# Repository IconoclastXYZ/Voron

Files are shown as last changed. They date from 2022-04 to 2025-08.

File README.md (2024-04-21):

# Voron
Build details, tips, tricks and traps for the 2.4 r1 - r2

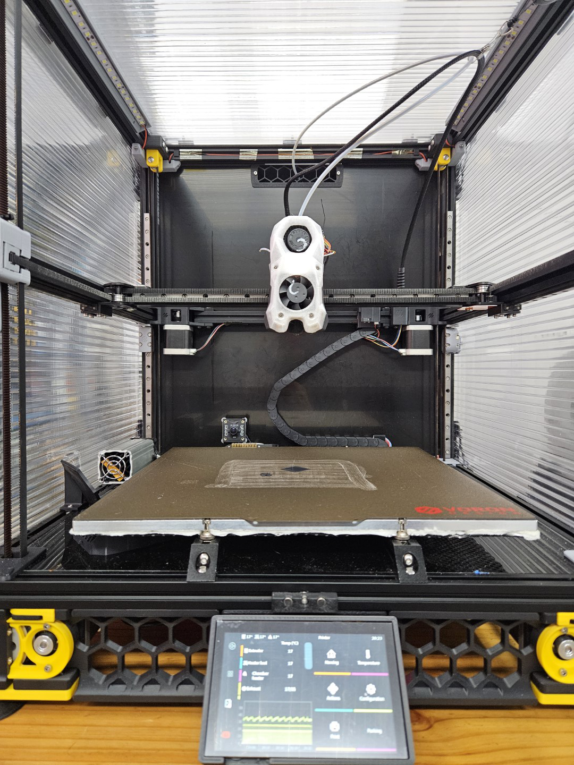
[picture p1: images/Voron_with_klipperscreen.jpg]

Closeup of the active heater with the angled air flow diverter
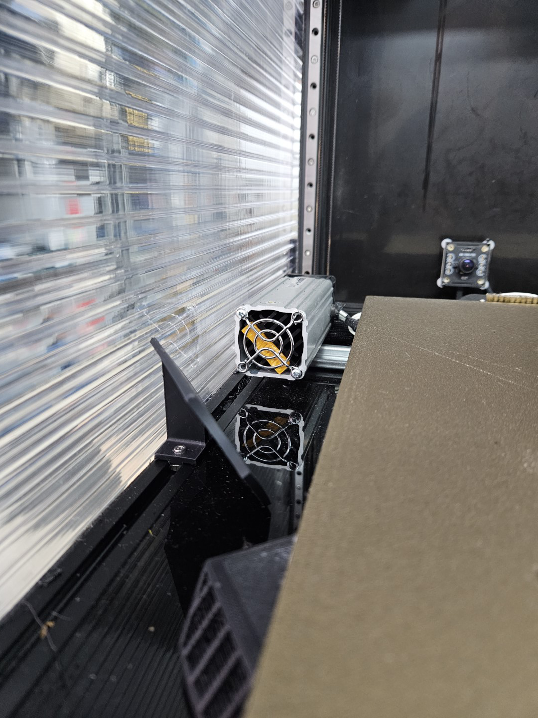
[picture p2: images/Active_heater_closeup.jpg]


With a hotmesh from the finished printer

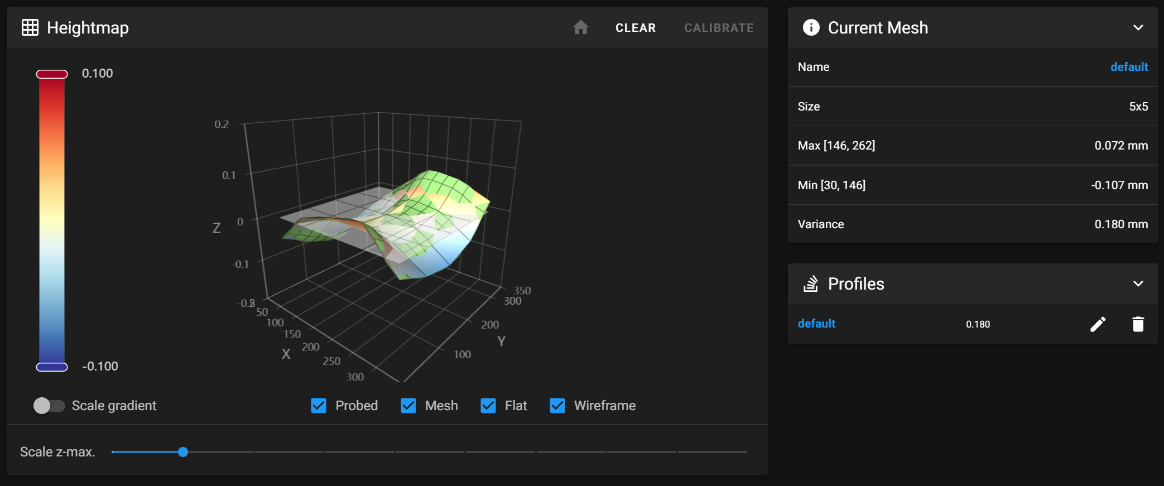
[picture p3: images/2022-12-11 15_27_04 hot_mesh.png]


## Base build from Formbot 3D kit - There were a few traps for young players in the Formbot 3D build, outlined [here](https://github.com/IconoclastXYZ/Voron/blob/main/articles/formbot_build.md)

## Things I wish I had known BEFORE starting to assemble the Voron
Lots of others build lists and hints exist, with my particular blind spots / learning points listed [here](https://github.com/IconoclastXYZ/Voron/blob/main/articles/build_lessons.md)
  
## [My current setup](https://github.com/IconoclastXYZ/Voron/blob/main/articles/my_setup.md)  

## Remember
- After each toolhead change (nozzle, fan replacement, heater change) run `PROBE_CALIBRATE` and remember to do it at a baked temp (nozzle 240, bed 95) and then do `TESTZ Z=-0.1` when happy with the paper test as Klipper assumes you do it [cold](https://docs.vorondesign.com/build/startup/#z-offset-adjustment)
  
## ToDo
- Fix the `controller_fan.py` script so that controller fans do not always come on with any stepper motor - to replace the kludge using a fake stepper motor
  
## Under consideration
- [Plug panel](https://github.com/tanaes/whopping_Voron_mods/blob/main/side_skirts/STLs/side_skirt-plug_panel-350.stl) for external connections to the Pi, but need to find out what the holes are sized for?
- [Full coverage heater pad](https://uniqueprints.shop/shop/buildplate/voron-keenovo-bed-heater-fermio/)
- [Custom heater plate with slot for top of plate temperature sensor](https://preciseprinterparts.com/voron-cast-aluminum-printer-bed-350mm-vor-ver-24-and-18.html)
- [Kinematic bed mount](https://github.com/tanaes/whopping_Voron_mods/tree/main/kinematic_bed)
- [FYSETC ultralight X rail](https://www.aliexpress.us/item/3256804719096286.html) with the appropriate mounting blocks from [here](https://github.com/GiulianoM/Fystec-Voron-X-Block), [here](https://www.thingiverse.com/thing:5671339) or [here](https://www.teamfdm.com/files/file/641-light-x-beam-mounting-block/), with the [M5 heat inserts](https://www.amazon.com/M5x5-8mm-OD7-1mm-Threaded-Plastic-Staking/dp/B08T9W17CR)
  
## Utility and Test prints
- Voron test cube
- [Andrew Ellis print tuning guide and parts](https://ellis3dp.com/Print-Tuning-Guide/)
- [Eric Zimmerman setup guides and Voron config](https://github.com/EricZimmerman/VoronTools)
- [X-rail belt clamps for installing the toolhead easily](https://www.printables.com/model/714602-voron24trident-ab-belt-clamps-reoriented-and-holes/files)
- [Filament swatches](https://www.printables.com/model/27814)
- [Bridging tests](https://www.thingiverse.com/thing:476845/files)
- [Temperature tower models](https://www.thingiverse.com/thing:2729076)
- [Hot end flow test generator](https://hotend-flow-tester.netlify.app/)
- [Pressure advance calibration pattern generator](https://realdeuce.github.io/Voron/PA/pressure_advance.html)
- [Variety of Wago mounts](https://github.com/VoronDesign/VoronUsers/tree/master/printer_mods/LoganFraser/WagoMounts)

## [Filament settings for the Voron](/filaments/Polymaker-filament-settings.md)
- Filament dryer (a must!) - [EIBOS 3D Filament Dryer CYCLOPES](https://www.eibos3d.com/cyclopes-detail) - there are quite a few alternatives, but none of them seem to work terribly well. This one regularly gets the filaments down to 20% RH
- Polymaker Polylite PA6-CF
- Polymaker Polylite ASA
- Polymaker Polylite PLA
- Polymaker Polylite PC

## Other resources
- [BTT Octopus pinout](https://github.com/VoronDesign/VoronUsers/tree/master/firmware_configurations/klipper/revnull/btt_octopus_pins)
- [Great article on the Octopus with lots of pinouts, etc.](https://3dwork.io/en/btt-octopus/)
- [BTT Schematic from Thomas White](/images/Octopus34-2048x1124.png)
- [Klipper config reference](https://www.klipper3d.org/Overview.html)
- [G-code Wiki](https://reprap.org/wiki/G-code)
- [Nero 3DP Tutorial video on deracking](https://www.youtube.com/watch?v=cOn6u9kXvy0)
- [Plating tool for optimising printing plates](https://github.com/Rhoban/Plater), but the Windows version needs to come from [here](https://drive.google.com/drive/folders/1USaJTZzJk_7KIQr8ctoPnoI9gQ6FYcY9) which was listed on the Issues page
- CloudCompare tool - finding differences in models / meshes (and lots more!) - https://www.cloudcompare.org/
- Voron mechanical construction manuals - [current and prior versions](https://docs.vorondesign.com/build/mechanical/#v2)
- [Great list of Voron Mods](https://github.com/Amarpal89/VoronUsers/tree/master/printer_mods)
- JINJA [Template Reference](https://jinja.palletsprojects.com/en/3.0.x/templates/) - used in klipper macros for additional control / automation

## Slicer information
- After trying them all (IdeaMaker, PrusaSlicer, Cura (various versions), others I can't remember) settled on SuperSlicer
- Using base profile from Andrew Ellis (pif profile) but customising for my printer and filaments

### Slicer tweaking
- Start slower than you would like, but Andrew's velocities are not bad at all
- Changed settings for overhangs to slow down much more and for PLA to cool agressively - much better overhangs
- Supports - automatic puts them *everywhere* which is a pain, paint them on only as required. Slower overhang head speeds are much better than removing lots more supports
- Suggested support settings from https://forum.prusa3d.com/forum/prusaslicer/prusaslicer-hard-to-remove-supports/
-- 0.25mm z distance.
-- 75% xy distance.
-- 3mm support spacing.
-- 4 interface layers.
-- 0.2mm interface layer spacing.
-- I think those are the key settings. Exposed support pulls off easily. Any entangled with the part (e.g. between legs) requires cutting to separate before pulling apart. 

These settings are working well for me with PLA and both 0.25 and 0.40mm nozzles. Haven't tried much else.

### Filament based settings
- Adjust the Z-offset based on the filament
- SET_GCODE_OFFSET Z_ADJUST=0.05 MOVE=1 - moves it up 0.05mmm, used for ASA on a hot bed in the Filament Custom G-code settings

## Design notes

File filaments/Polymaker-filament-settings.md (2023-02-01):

# Polymaker Filament settings for the Voron 2.4r2

| Setting | PA6-CF | ASA | PLA | PC-Clear  | PolyWood |
|---|---|---|---|---|---|
| Filament | | | | | |
| Extruder (first) | 280 | 240 | 200 | 260 | 185 |
| Extruder (other) | 275 | 240 | 195 | 260 | 185 |
| Bed (first) | 35 | 95 | 65 | 105 | 45 |
| Bed (other) | 35 | 95 | 60 | 105 | 45 |
| Chamber (C) | 25 | 40 | 0 | 40 | 0 |
| Extrusion X | 0.924  | 0.924 | 0.924 | 0.924 | 1.1 |
| Density | 1.17 | 1.03  | 1.03? | 1.03? | 0.8 |
| Cooling | | | | | |
| Default fan | 0% | 0 | 80 | 0 | 100 |
| Bridge fan | 50% | -1 | 100 | 20 | 100 |
| Short layer fan if time under | 20s | 20 | 60 | 0 | 100 |
| Max fan | 0% | 0 | 100 | 100 | 100 |
| V short layer time goal | 15s | 15 | 15 | 15 | 15 |
| Max speed reduction | 90% | 90 | 90 | 90 | 90 |
| Min print speed | 10mm/s | 10 | 10 | 10 | 10 |
| Filament overrides | | | | | |
| Retraction length | 2.6mm  | - | - | - | 4mm |
| Wiping | | | | | Retracting |
| Z_offset | 0.025mm| | | | |
| Bridge flow | 40% | | | | |

## Other settings for all filaments

- All as per Andrew Ellis profile except
-- Bridge speed - 60mm/s
-- Flow ratio - bridge - 70%

## Learning curve notes
### PA6 CF - Polymaker
- Drying - !!!!! >10 hours at >50C !!!!!
- Squish - 0.025mm less than standard bed zeroing is not a bad start (for comparison, ASA likes more, so 0.025mm the other way)
- Speed - much lower than PLA & ASA - so generally 30-40mm/sec, otherwise the surface finish is awful
- Pressure advance - way difference than ASA (0.055, smoothing 0.020), instead use 0.150 with a 0.040 sec smoothing time
- Retraction - very important, and much higher - 6 mm works well
- Wiping - also very important - 50% before retraction and then especially when crossing perimeters
- Bridges - the other hard part with PA6 CF - reduce flow to 60% on the bridge and 75% above it, speed 30mm/sec, bridge line density min 50%, max 60%
- Perimeters on bridges - choose 'Fill the voids with bridges' for the 'no_perimeter_unsupported_algo'
- Z-hop (Lift Z on Superslicer) - turn off, otherwise it strings / bulges
- Cooling - full fan speed for bridges only

- Example with slow print speeds, but not optimised for PA, retraction or bridging (70% flow on left, then 5% decreases to reach 45% on right)
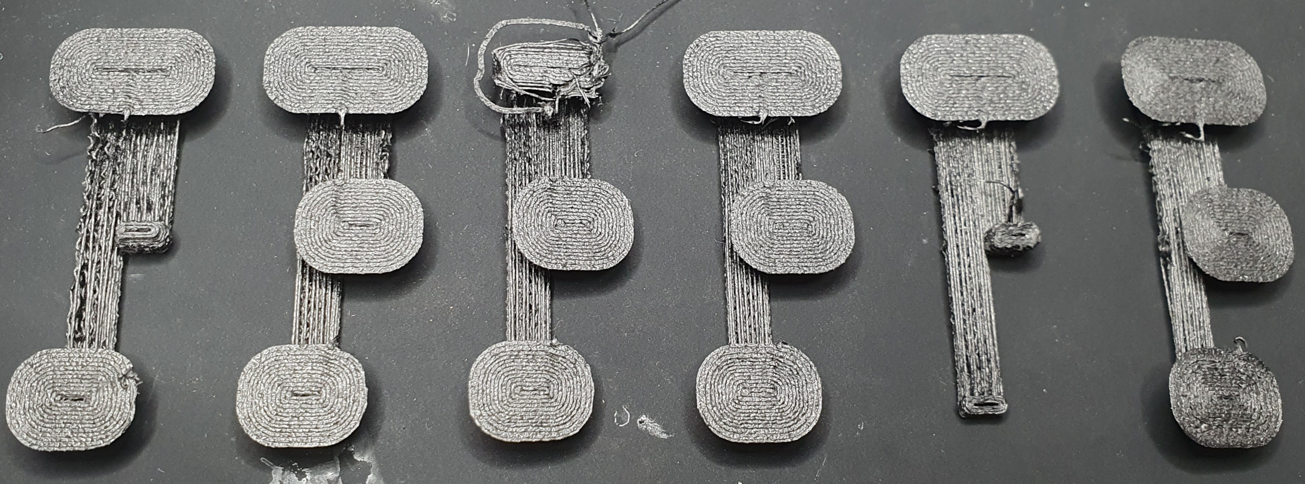
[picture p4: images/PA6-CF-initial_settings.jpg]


 - Example partially optimsed
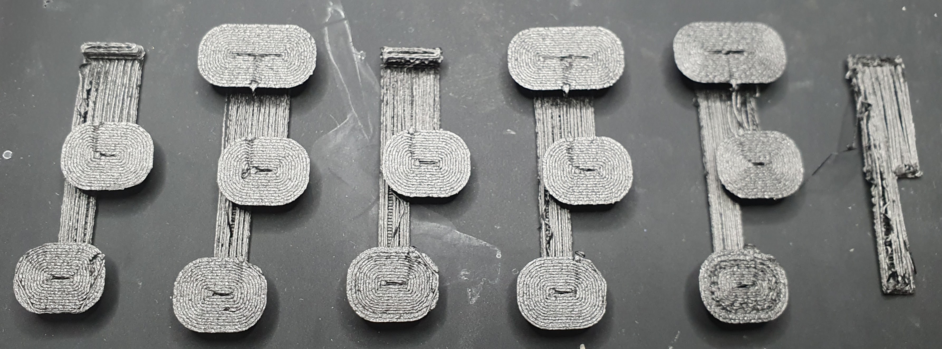
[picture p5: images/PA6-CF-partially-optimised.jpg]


- Example fully optimised, seems best at ~50-55% flow
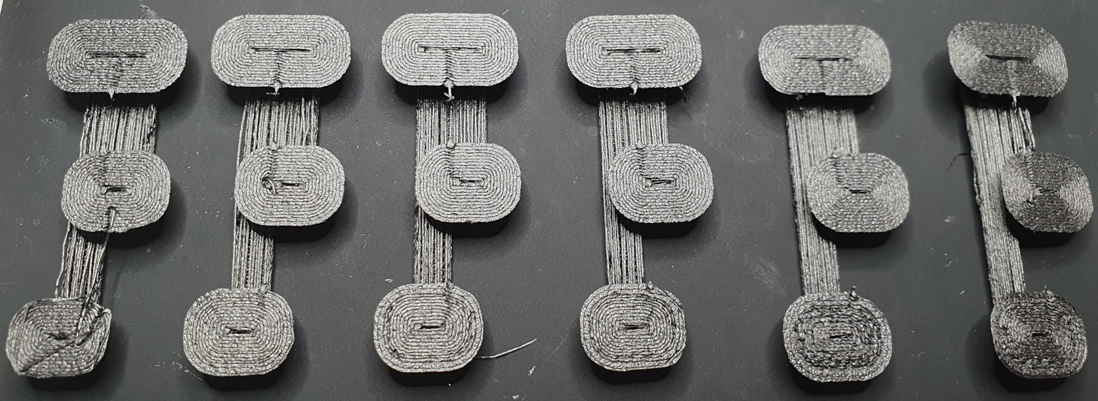
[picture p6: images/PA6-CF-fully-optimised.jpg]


- Examples of Voron test cubes, left in ASA, then same settings for PA6 CF (apart from slower speeds), gradually improving as retraction is increased, then not cross perimeters, then finally bridging is optimised on the right
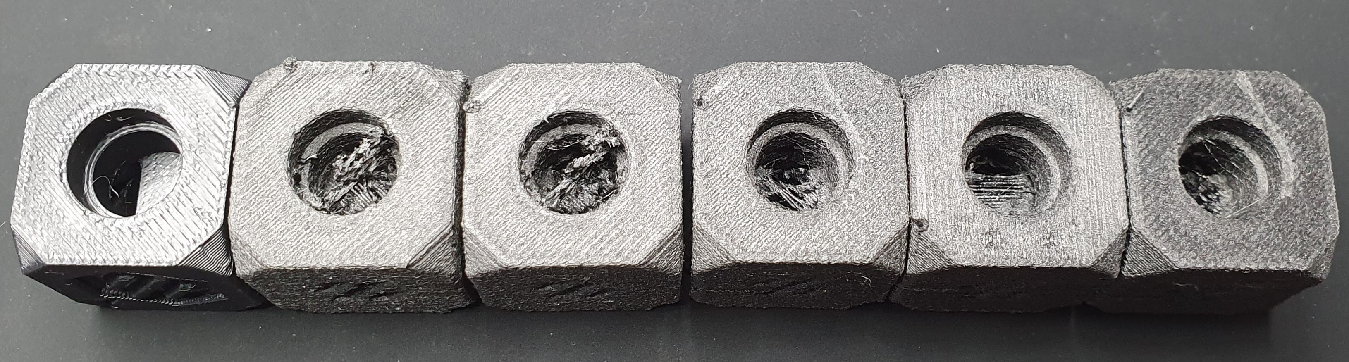
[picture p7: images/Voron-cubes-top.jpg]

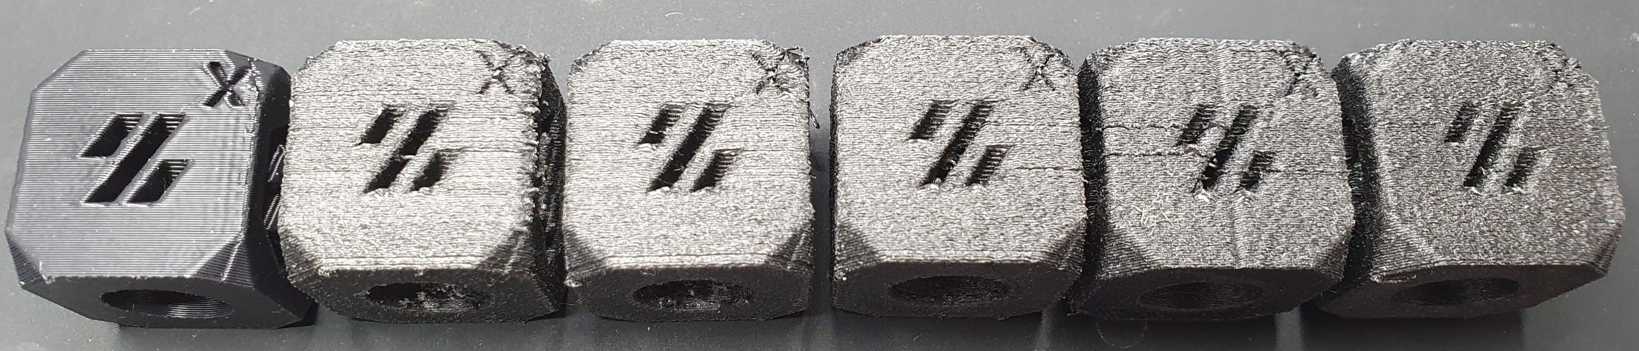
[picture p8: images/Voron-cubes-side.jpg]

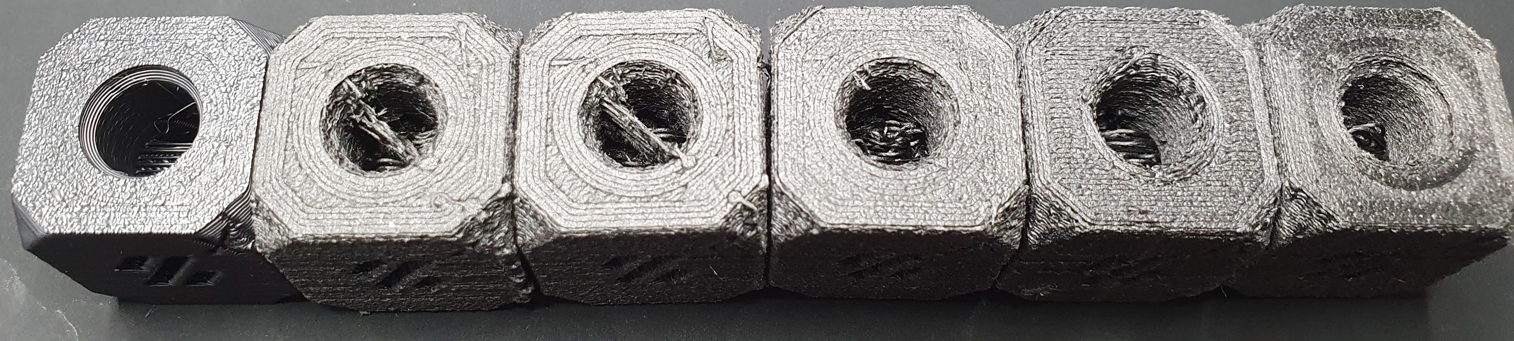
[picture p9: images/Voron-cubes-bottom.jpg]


### Final thoughts on the PA6 CF
- I went back to the drawing board, because even after *lots* of optimisation:
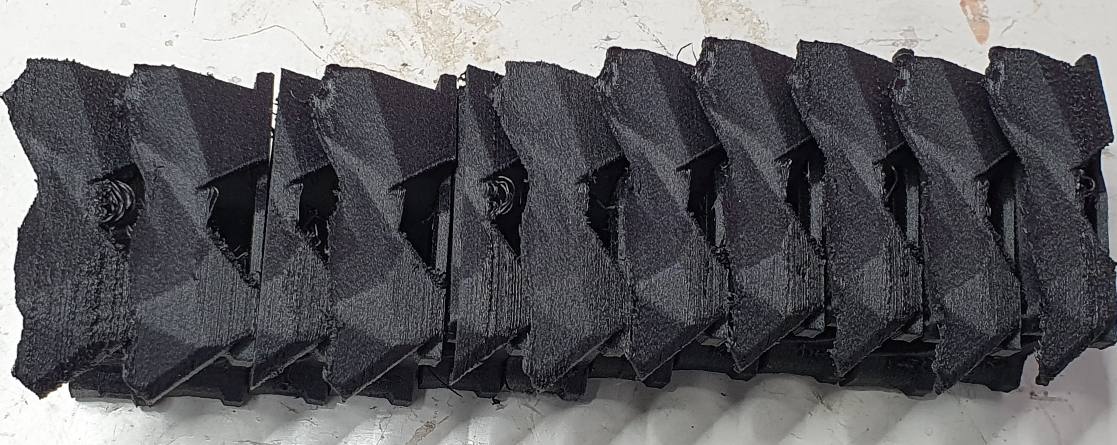
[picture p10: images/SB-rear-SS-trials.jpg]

-  the best I could get on the Stealthburner rear (which is a very challenging part because of its complex shape, relatively long bridges, lots of holes and then a narrow fin that sticks up) was this:
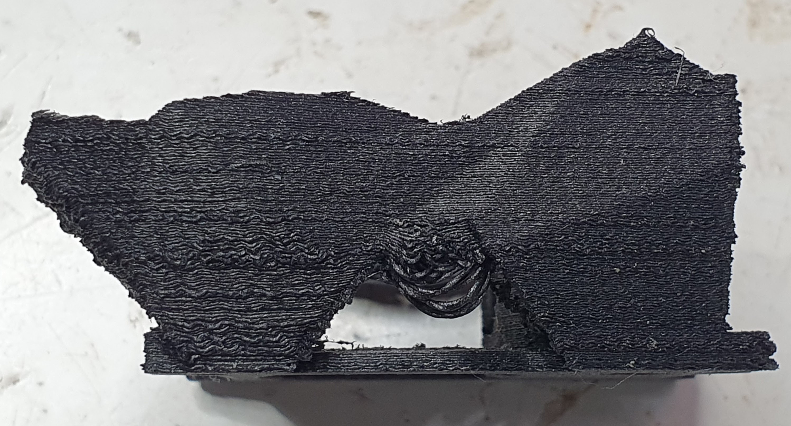
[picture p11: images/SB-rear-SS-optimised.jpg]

- As you can see, the bridges sag, the surface finish is awful, and it gets worse on the fin

- I went to PrusaSlicer with a fresh setup and it (and the test cubes) got much better:
- But there were still issues with the uneven surface finish and also blobs
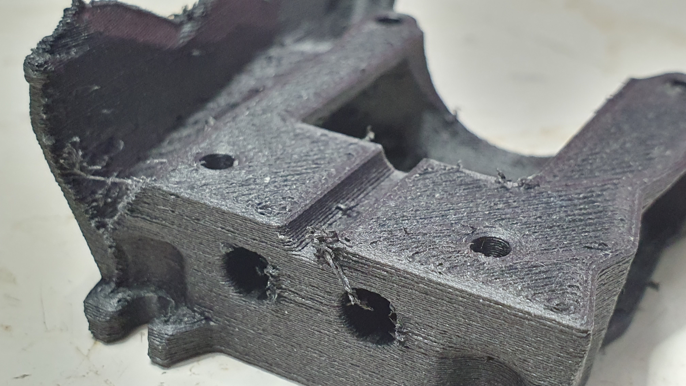
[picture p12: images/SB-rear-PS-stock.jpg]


- Finally I worked out the two key issues:
1. PA6 CF does not like to print slow. The surface finish gets *much* better going from 25mm/s to 50mm/s for the external perimeter
2. It does not like changing speed. Using the automatic slow-down to adjust for small layers makes it really bad - probably mostly because it makes it slow again
3. It does not like to change volumetric speed fast - using `max_volumetric_extrusion_slope_negative = 1.8mm/s^2` cleaned it up considerably, but not perfect
4. Retraction - Polymaker says 3-4mm at 50-60mm/s. This gave lots of blobs and ruined otherwise good looking prints. Instead 0.75mm at 30mm/s and NO z-hop (`retract_lift` on superslicer) cleaned it all up
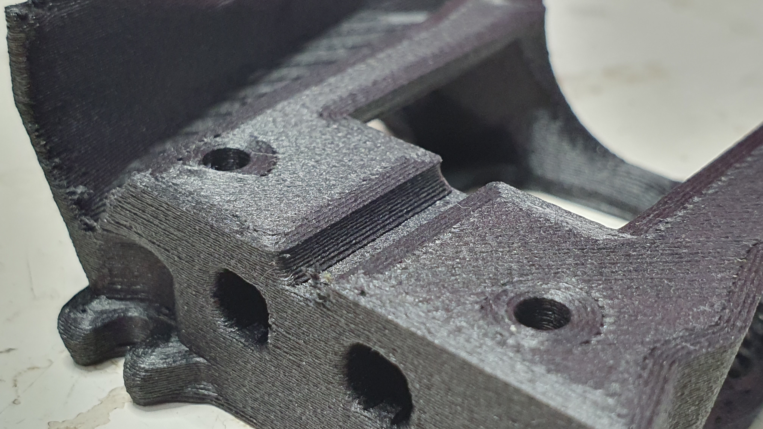
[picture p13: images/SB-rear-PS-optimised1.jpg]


- Key settings
1. Temperature - Extruder - 280C, Bed - 35C, Chamber - 0
2. Extruder - retraction length - 0.75mm, Lift Z - 0, Retraction/deretraction speed 30mm/s, Wipe on retracting by 50%
3. Filament - cooling - 100% on bridges, otherwise 0%, max volumetrix speed 11mm^3/s, but never gets close, PA - 0.080, PA smooth time 0.040
4. Print - infill gyroid, ensure vertical shell thickness, avoid crossing perimeters, detect bridging perimeters, seam rear, external perimeters first, Arachne
5. Speed - Perimeters 100, small 50, external 50, infill 125, solid 120, top solid 50, bridges 60, gap 40, first layer 30
6. Acceleration - perimeters 2000, infill 4000, bridge 3000, first layer 1000
7. Pressure equalizer - max slope negative 1.8
8. Bridge flow 0.8, Infill perimeter overlap 20%
9. Extrusion widths - standard PrusaSlicer
10. Output options - label objects

### Other filaments
- Most of the other filaments can cope with quite fast printing, especially for fill

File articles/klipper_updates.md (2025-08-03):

# Simplying MCU klipper updates
How to update klipper on the different MCUs in the system after updating it on the Raspi

## Update the controller board - BTT Octopus 1.1
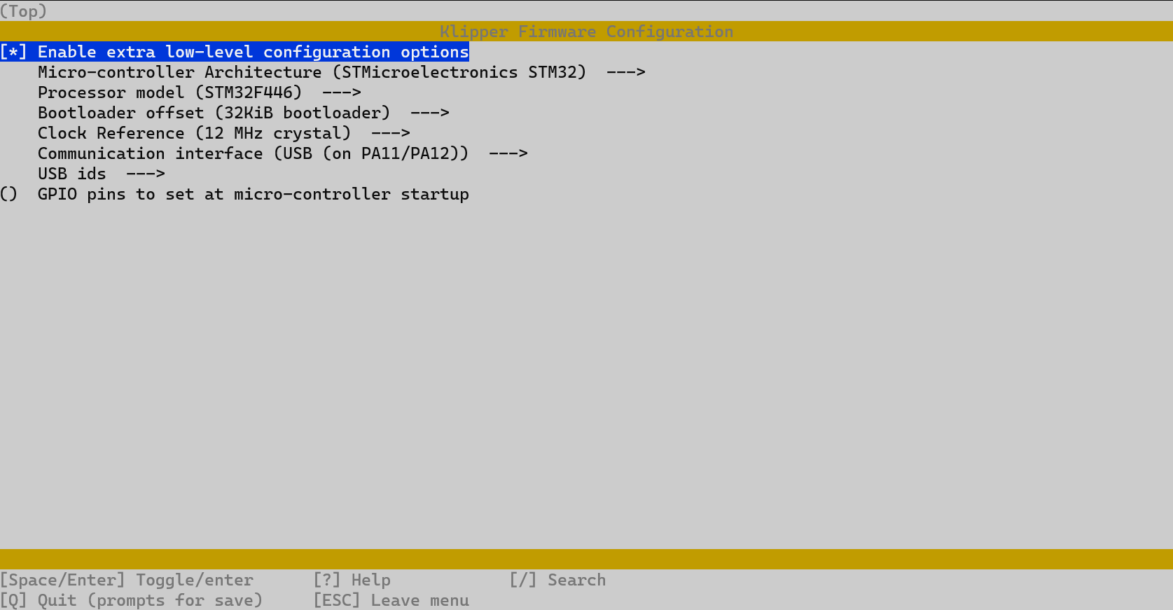
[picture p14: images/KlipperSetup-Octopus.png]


```
cd ~/klipper/
make clean KCONFIG_CONFIG=config.octopus
make menuconfig KCONFIG_CONFIG=config.octopus
make KCONFIG_CONFIG=config.octopus

sudo service klipper stop
make flash FLASH_DEVICE=/dev/serial/by-id/usb-Klipper_stm32f446xx_Octopus1_1-if00
sudo service klipper start
```

## Update the Toolhead board - Orbitool O2S
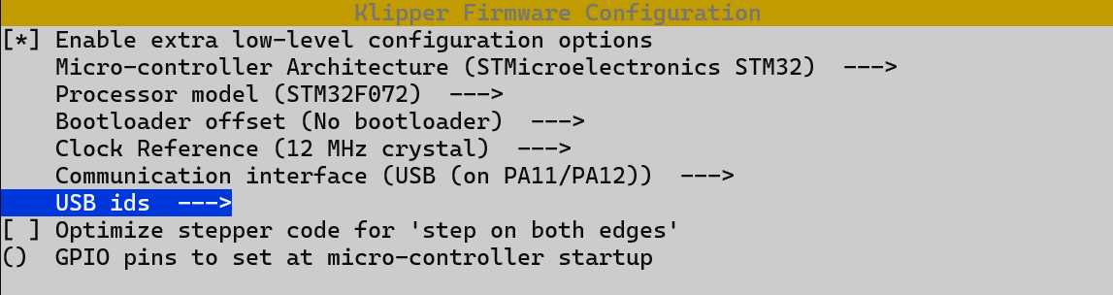
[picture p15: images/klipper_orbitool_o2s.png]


```
cd ~/klipper/
make clean KCONFIG_CONFIG=config.orbitool
make menuconfig KCONFIG_CONFIG=config.orbitool
make KCONFIG_CONFIG=config.orbitool

sudo service klipper stop
make flash FLASH_DEVICE=/dev/serial/by-id/usb-Klipper_stm32f072xb_Orbitool_O2S-if00
sudo service klipper start
```

## If these methods do not work...
You might need to put the Octopus into DFU mode using the onboard jumper - https://www.sanketsjournal.com/articles/20240303-flashing-btt-octopus-pro-with-klipper-using-pi

Look for devices to flash using `lsusb` and when they are flashed `ls /dev/serial/by-id`
Then flash them with either:
`make flash FLASH_DEVICE=0483:df11` (if from DFU mode)
`make flash FLASH_DEVICE=/dev/serial/by-id/usb-Klipper_stm32f072xb_Orbitool_O2S-if00` (if in normal mode)

More details on the Orbitool flashing are [here](file:///D:/Download/Orbitool%20O2S%20User%20Manual.pdf)

# Historical approach
When I was using CanBUS to communicate with the toolhead

## Learning points...
- I started the CANBus journey with the WaveShare RS485-CAN-HAT and although there are comments to the contrary it worked well and was stable, with a bus speed of 250000 bps (baud)
- I needed to change away from the WaveShare as I wanted to install the KlipperScreen mod, and the Waveshare board neatly part covers the screen connector on the RasPi
- Rather than have _yet another controller board_ I opted to do the CANBus over USB solution on the Octopus 1.1. It is a bit of a fiddle to setup because:
1. you need an RJ11 connector - found an old telephone cable and butchered it
2. you need canboot loaded on the Octopus - then Klipper is loaded over the top of it - done

- Problem comes when you want to update Klipper as it cannot be done directly over serial as before since the Octopus is not directly connected to the RasPi, but rather through CANBus. Therefore a *bunch* of solutions are proposed on the internet to work around this, double tap the reset button, suspend Klipper startup _just_ as the RasPi starts, etc. None worked reliably for me. In the end, lift up the printer, connect the jumper across the boot pins, restart the printer, reinstall CanBoot, then reinstall Klipper. Yuck!
- After doing that a few times, then having the EBB no longer be found it was too much, so off to BTT U2C school. This little controller is cheap, but the current version has PROBLEMS and I eventually found this guide from [Eric Zimmerman](https://github.com/EricZimmerman/VoronTools/blob/main/EBB_CAN.md) on how to perform the necessary miracles and make it work.
- Of course it hard coded firmware from BTT has a bus speed of 1000000, so a few long USB cables later, the EBB36 is reflashed with CanBoot and Klipper and everything is talking again.

## Then the BTT EBB CANBus Board - directly with WaveShare or U2C
## Be sure to choose speed of 1000000 not 250000!!!
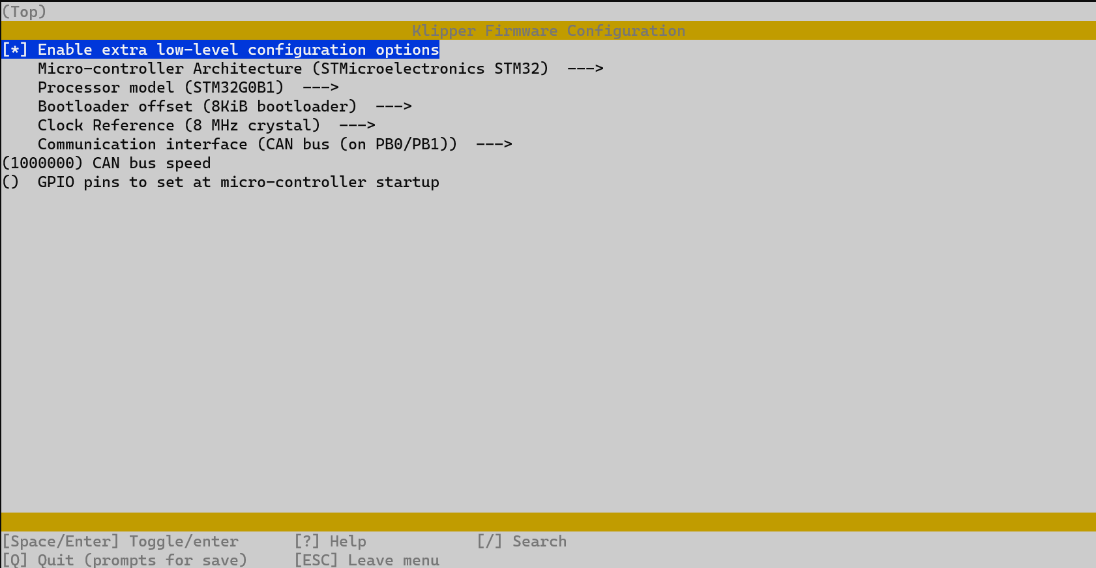
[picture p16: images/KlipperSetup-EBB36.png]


- making sure you choose the right version as the CANBus pins have changed between [versions](https://github.com/bigtreetech/EBB)
- after setting it up with [CANBoot](https://github.com/Arksine/CanBoot), explained [here](https://www.youtube.com/watch?v=_FELCN8CbWA):
```
cd ~/klipper/
make clean KCONFIG_CONFIG=config.ebb
make menuconfig KCONFIG_CONFIG=config.ebb
make KCONFIG_CONFIG=config.ebb

mv ~/klipper/out/klipper.bin ~/firmware/EBB_1.2_klipper.bin

cd ~/CanBoot/scripts
python3 flash_can.py -i can0 -f ~/firmware/EBB_1.2_klipper.bin -u d3e7f0c00d1a
```
- Just remember that sometimes the Pi will not find the MCU after a service stop and new make, requiring a power cycle of the whole system - much time wasted figuring this one out!

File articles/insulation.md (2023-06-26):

# Stats on insulation acrylic vs polycarbonate twinwall
For U-values, lower is better

# Twinwall polycarbonate sheet
- 8mm - U-value 3.3
- 10mm - U-value 2.9
- Ref: https://vicwest.com/wp-content/uploads/2019/07/SUNLITE_En_Technical_Guide_61353_Web_1.pdf
- Melting point >260&deg;C, glass transition ~147&deg;C

# Perspex / acrylic
- 3mm - U-value 5.2
- 5mm - U-value 4.9
- Ref: https://www.allplastics.com.au/component/docman/doc_download/93-allplastics-perspex-datasheet-for-glazing-pdf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
- Melting point ~160&deg;C, glass transition 90-105&deg;C

# Final choice...
- I went with the 8mm Polycarbonate Twinwall - affordable from a hardware store, easy to work with (cuts with a craft knife) and mount with these clips from [Annex Engineering](https://github.com/Annex-Engineering/Annex-Engineering_User_Mods/tree/main/Printers/All_Printers/annex_dev-Panel_2020_Clips_and_Hinges)
- Even with the active heating, the outside of the Twinwall panels are cool while the perspex doors are warm/hot
- The higher melting point (and glass transition) of the polycarbonate makes it a safer bet to have a heater sitting beside it

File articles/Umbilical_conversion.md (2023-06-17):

# Converting to an Umbilicus rather than drag chains

## What is needed to change
- Swap to CanBUS
- Move x-endstop to toolhead
- Move y-endstop to A-motor mount
- Make end mounts for the umbilicus

## CanBUS hardware
- Need a controller board to drive from the Raspi - [WaveShare CanBus adaptor](https://learn.sb-components.co.uk/RS485-CAN-HAT)
-- Now people recommend the BTT U2C board instead, explained [here](https://wiki.kb-3d.com/home/canbus_guide)

- CAN Bus board from [BigTreeTech](https://www.aliexpress.com/item/1005004243374113.html) with the [GitHub and manual](https://github.com/bigtreetech/EBB/)
-- Ended up using the BTT EBB36 1.2 with a [canbus mount](https://github.com/KayosMaker/CANboard_Mounts)
-- With a great introduction on how to flash the firmware and wire it up [here](https://wiki.kb-3d.com/en/home/btt/voron/BTT_EBB36)
- Final wiring for the EBB36 board
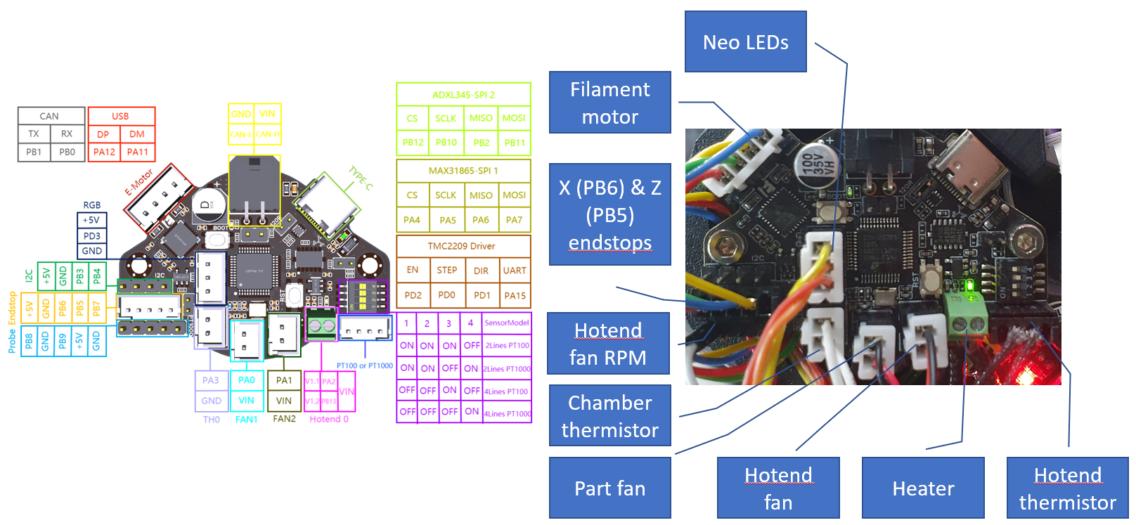
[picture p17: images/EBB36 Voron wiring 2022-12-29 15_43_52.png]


- To setup the WaveShare RS485-CAN-HAT it is a little complicated, but best described [here](https://github.com/maz0r/klipper_canbus/blob/main/controller/rs485.md)
- Make sure to choose the same bus speed for the CAN-HAT (suggest 250000) and the EBB36 (when flashing it)

- Add to /boot/config.txt (note the need for the \[all\] otherwise it can slip under Pi2, Pi3 or Pi4 and not work
```
[all]
dtparam=spi=on
dtoverlay=mcp2515-can0,oscillator=12000000,interrupt=25,spimaxfrequency=2000000
```
- With more info on how to setup CAN Bus [here](https://www.klipper3d.org/CANBUS.html)
- Or a great complete guide on the BTT EBB36 and U2C process [here](https://github.com/EricZimmerman/VoronTools/blob/main/EBB_CAN.md)

- Honestly, easier just to use the BTT U2C now - also its interface is much faster than the RS485-CAN-HAT

### Using the BTT Octopus 1.0/1.1 as the CanBUS
- Great guide on the Octopus+Pi+2040 from [akhamar](https://github.com/akhamar/voron_canbus_octopus_sb2040)
- Or a more general guide which came from a source unknown on Facebook with a [PDF](/articles/How%20to%20Use%20CAN%20Toolhead%20Boards%20Connected%20Directly%20to%20Octopus.pdf)

## Moving x-endstop
- Built-in mount point on the new Stealthburner design

## Moving y-endstop
- [No need to reprint the A-motor mount](https://github.com/VoronDesign/VoronUsers/tree/master/printer_mods/Minsekt/Rear_Umbilical/Y_Endstop_Relocation)
- [Alt - no need to reprint the A-motor mount](https://github.com/RepRapster/Voron2.4-Rear-Gantry-Y-Endstop-Mount) - also reduces the offset required
- [Reprint of A-motor mount required](https://github.com/VoronDesign/VoronUsers/tree/master/printer_mods/hartk1213/Voron2.4_Y_Endstop_Relocation)

## Umbilicus mount for toolhead
- [Designed for Stealthburner](https://github.com/majarspeed/Misc-Voron/tree/main/StealthBurner%20Umbilical%20cover)

## Umbilicus mount for A-motor
- [No need to reprint the mount](https://github.com/VoronDesign/VoronUsers/tree/master/printer_mods/Minsekt/Rear_Umbilical)
- And a cleaner one [here](https://www.printables.com/en/model/412460-voron-24-a-drive-pg7-umbilical-mount-with-cable-cu)

## Cable end protectors
- [PG7 cable glands at each end](https://www.amazon.com.au/gp/product/B08K8FB4KV/ref=ppx_yo_dt_b_asin_title_o02_s00?ie=UTF8&th=1)
- Mod the end mounts to include a thread for the cable gland (1/2-20 UNF thread)

## Moved the Z chain to be underslung, saving space out the back
- [Various versions for canbus](https://www.printables.com/model/279739-voron-can-bus-z-chain-move/files)

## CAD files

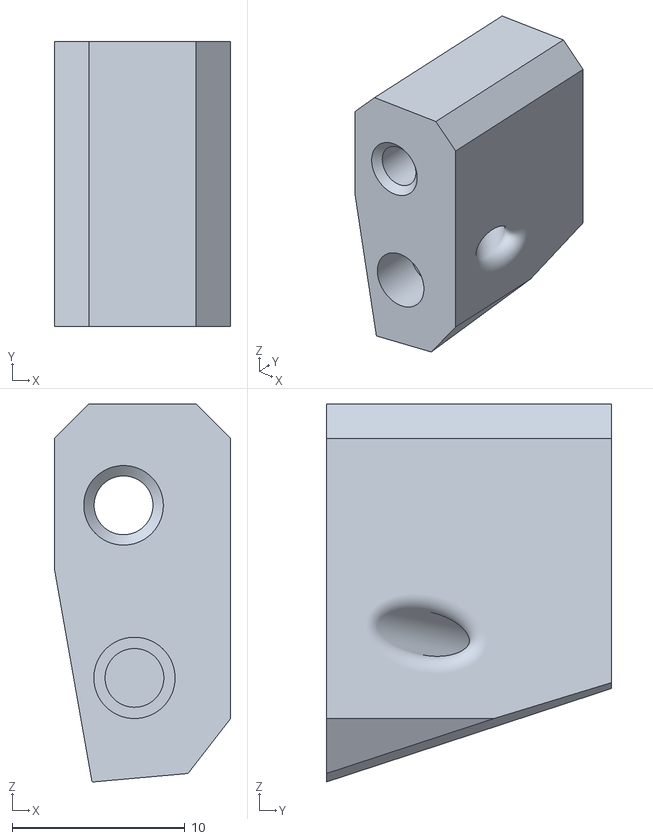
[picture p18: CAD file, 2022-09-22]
articles/Chamber thermistor carriage mount.stl
10.2 x 16.5 x 21.9

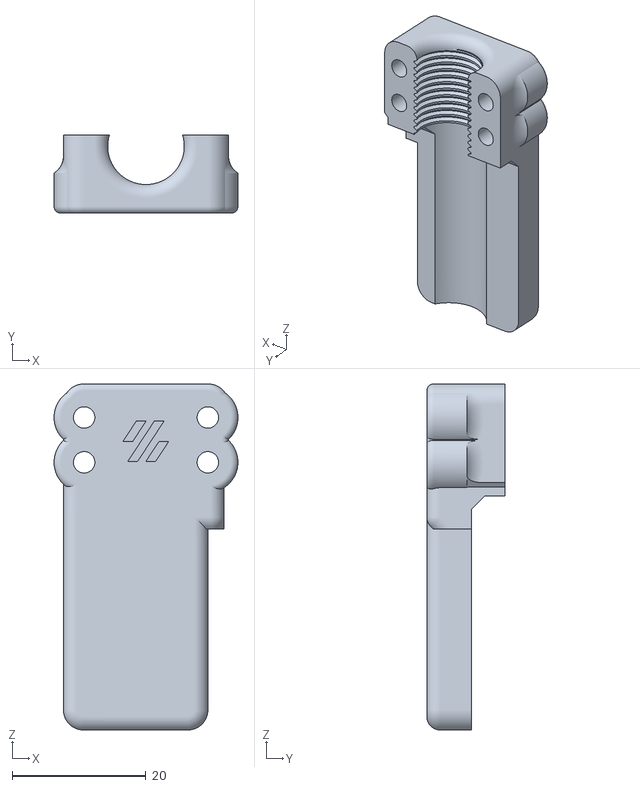
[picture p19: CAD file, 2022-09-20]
articles/Threaded rear umbilicus mount.stl
27.5 x 11.7 x 51.7

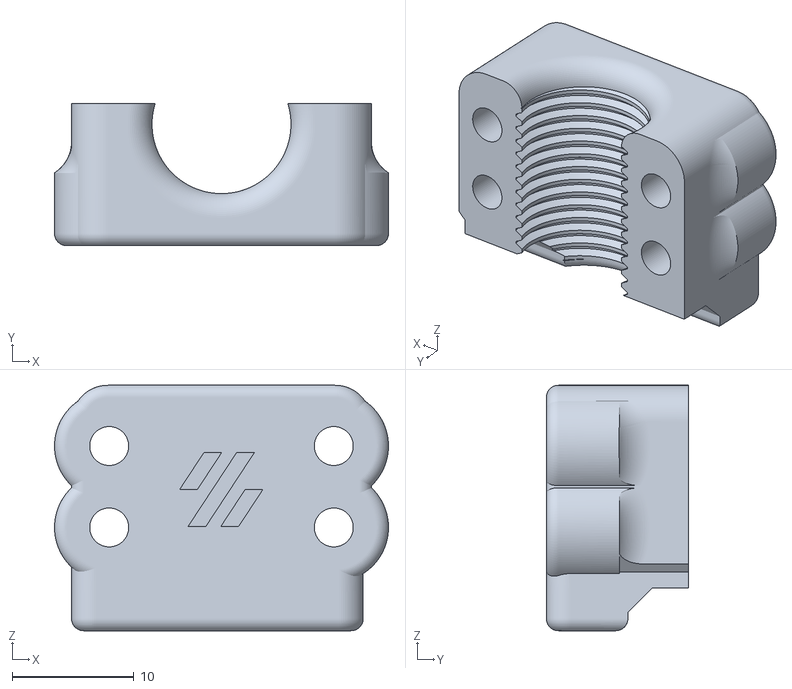
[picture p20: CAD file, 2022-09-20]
articles/Threaded Cover clamp front umbilicus.stl
27.5 x 11.7 x 20.2

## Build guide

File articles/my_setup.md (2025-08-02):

# My Setup
## Base build - Voron V2.4 350mm (with mostly r2 parts)
### Formbot 3D kit - supplied to 2.4r1 specs but with
- hall effect XY endstops - changed to microswitches for reliability
- z endstop circuit board - gone with the Voron Tap
- Phaetus Dragon HF hotend - changed to Phaetus Rapido
- [BigTreeTech Octopus 1.1](https://www.biqu.equipment/products/bigtreetech-octopus-v1-1)
- Raspberry Pi 3B+ (1GB RAM) - changed to RPi 4 4GB
- [KlipperScreen](https://klipperscreen.readthedocs.io/en/latest/) using a BigTreeTech PI TFT50 display mounted using [this guide](https://wiki.kb-3d.com/en/home/btt/voron/PITFT50)

### Printed parts
- Third party (Etsy) printed parts in ASA to 2.4r1 with a few extra needed for the MGN12H rail
- Turns out that they spontaneously printed the new (r2) din rail mounts for components, which is great
- Quite a few other parts from r2 can be printed for r1 kits and only improve them, eg. z-axis and ab-axis idlers, all the skirts, all electronics mounts

## Toolhead
### Current setup
- Phaetus Rapido Plus hotend - with integrated 115W heater and P1000 thermistor
- [Beacon 3D - rev H](https://beacon3d.com/) eddy current probe with [this setup](https://docs.beacon3d.com/quickstart/)
- [Umbilicus](https://github.com/IconoclastXYZ/Voron/blob/main/articles/Umbilical_conversion.md)
- [Bowden tube support, doubling as CANBus support](https://github.com/Exerqtor/Voron/tree/main/Mods/trident_ptfe_support-v2)
- [DragonBurner](https://github.com/chirpy2605/voron/tree/main/V0/Dragon_Burner)
- Using the [Orbiter 2.0](https://www.orbiterprojects.com/orbiter-v2-0/) and now the [Sensor v2](https://www.orbiterprojects.com/smart-sensor-for-orbiter-v2/) instead of the BTT runout sensor
- Upgraded the Orbiter to v2.5 with new extruder components
- Controller board - [Orbitool O2S](https://github.com/RobertLorincz/Orbiter-Toolboards/tree/main/Orbiter%20O2S%20Toolboard)
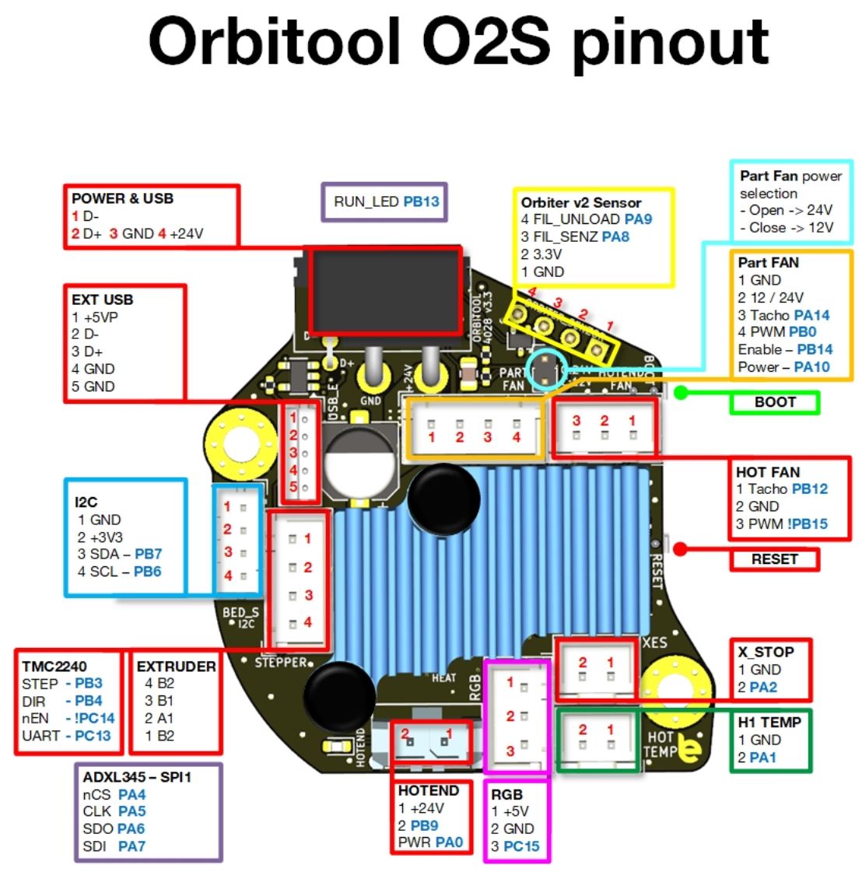
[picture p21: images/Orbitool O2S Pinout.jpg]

Orbitool O2S board pinout

### Previous setups
- Stealthburner and clockwork 2 - https://vorondesign.com/voron_stealthburner using and LDO motor
- [Voron Tap](https://github.com/VoronDesign/Voron-Tap) endstop and z-probe
- 3 wire hotend fan with [RPM monitoring](https://www.klipper3d.org/Config_Reference.html#heater_fan) and using the guide from Andrew Ellis and the linked [macro](https://ellis3dp.com/Print-Tuning-Guide/articles/useful_macros/hotend_fan_monitoring.html), with more info [here](https://forum.vorondesign.com/threads/ebb36-3-wire-fan-speed.83/), which explained why the first time I did it it blew the BTT EBB36 board. Now it has a signal diode inline with the endstop pin. Otherwise, the endstop supplies 7.8mA constantly, which is enough to drive the fan. A 5K resister drops this to 1.8mA but it then does not sense rotation.
- Orbiter 2.0 extruder and used this [modified stealthburner cover](https://www.printables.com/model/345237-voron-stealthburner-orbiter-v20/files) and [mount](https://github.com/sneakytreesnake/StealthOrbiter) and [this](https://www.printables.com/model/316984-ebb36-mount-with-cable-strain-relief-for-the-orbit) or [this]() mount for the EBB36 board. Alternatively use [this](https://github.com/elcrni/Voron-Mods/tree/main/Orbiter_2.0_SB_CW2_Enclosed) enclosed cover
- Controller board - [BTT EBB36](https://github.com/bigtreetech/EBB/tree/master/EBB%20CAN%20V1.1%20and%20V1.2%20(STM32G0B1))
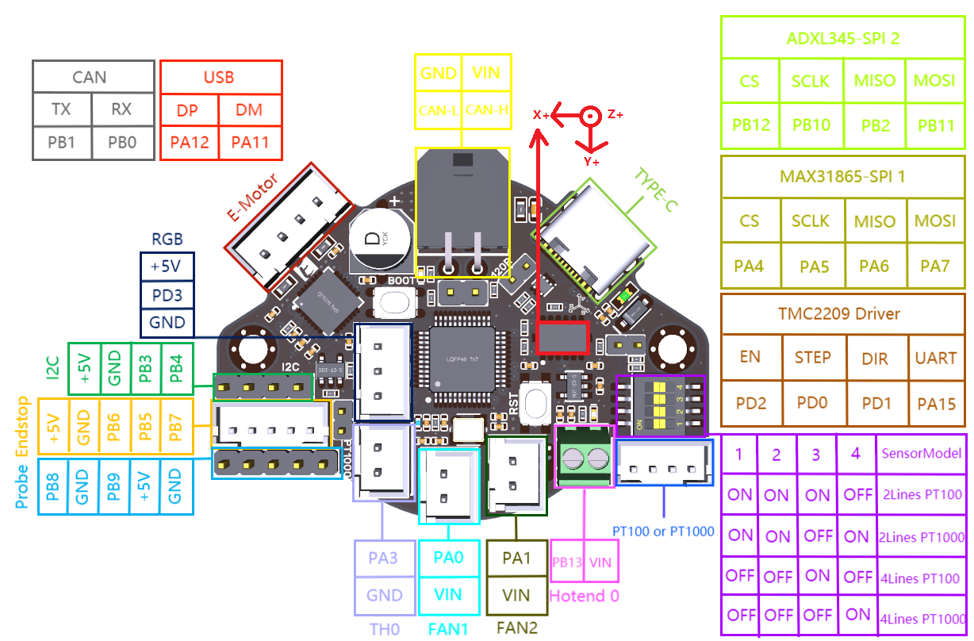
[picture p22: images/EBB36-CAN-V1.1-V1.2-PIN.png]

EBB36 wiring pinout

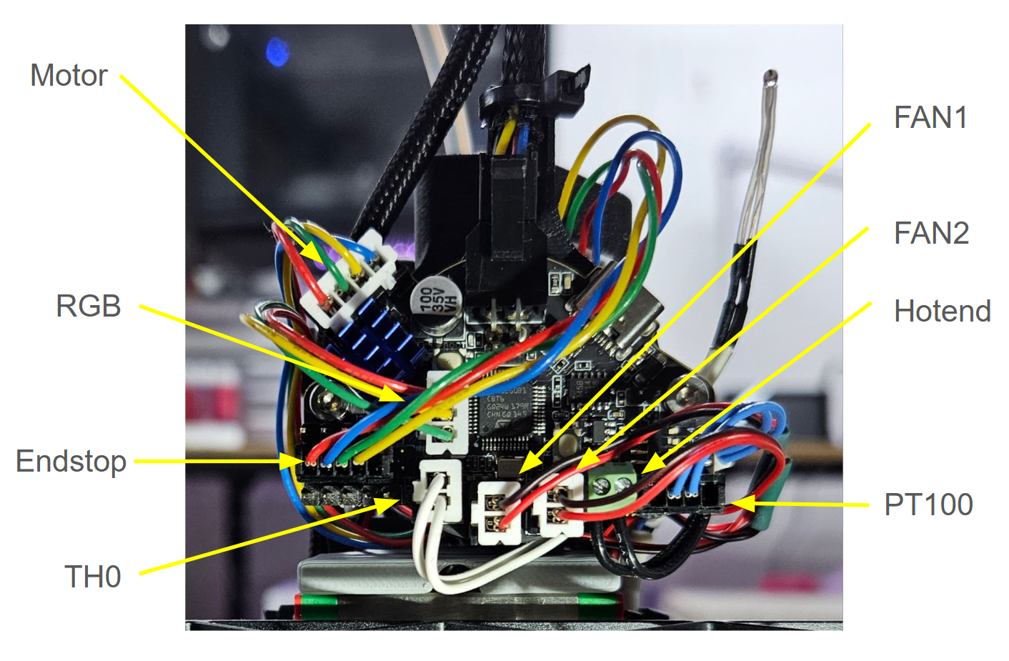
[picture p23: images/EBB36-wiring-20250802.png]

In place with cables

## Print axes
- MGN12H single X rail with reprinted parts to suit
- [Z axis tension mod from Edward Yeeks](https://github.com/edwardyeeks/VoronUsers/tree/master/printer_mods/edwardyeeks/V2.4_z_drive_motor_tensioner_mod)
- [Pin mod for gantry](https://github.com/VoronDesign/VoronUsers/tree/master/printer_mods/hartk1213/Voron2.4_Trident_Pins_Mod) - but just did the xy for now
- [Replace front z idlers with Rama design](https://github.com/Ramalama2/Voron-2-Mods/tree/main/Front_Idlers) but could have used the new design from [2.4r2](https://github.com/VoronDesign/Voron-2/tree/Voron2.4/STLs/Gantry/Front_Idlers)
- Change Z mount to use [spherical bearings](https://github.com/VoronDesign/VoronUsers/tree/master/printer_mods/hartk1213/Voron2.4_GE5C), tried IGUS, but too much stiction so using metal ones. Could have used nylock nuts (per Andrew Ellis) - now there is no friction on z-adjust. Checked the original parts and they had significant wear / catch marks!
- [Gantry backing bars](https://github.com/tanaes/whopping_Voron_mods/tree/main/extrusion_backers) to stop bimetallic strip effect and warping, purchased on [AliExpress](https://www.aliexpress.com/item/1005003779041015.html?spm=a2g0o.order_list.0.0.21ef180202r18o), also need new [XY chain riser](https://github.com/tanaes/whopping_Voron_mods/blob/main/extrusion_backers/STLs/XY_cable_chain_bridge-3hole-3mm_backer.stl) or some washers 

## Chamber
- Polycarbonate twinwall (8mm) side and top panels ([much better insulation than 3mm acrylic]( https://github.com/IconoclastXYZ/Voron/blob/main/articles/insulation.md))
- Active heating using a [DBK FGC1515.2R CIRRUS 230W Rail 115/230V Heater](https://dbkusa.com/collections/ptc-enclosure-fan-heaters/products/cirrus40?variant=39257500516410), controlled using a second solid state relay
- [Quick removable side / top panel clips](https://github.com/Annex-Engineering/Annex-Engineering_User_Mods/tree/main/Printers/All_Printers/annex_dev-Panel_2020_Clips_and_Hinges)
- [Removeable front hinges](https://github.com/VoronDesign/VoronUsers/tree/master/printer_mods/ElPoPo/RemovableDoors) - but use the old engineering trick of a longer screw in the bottom hinge so that they are much easier to get back on
- [Sturdy handles](https://github.com/VoronDesign/VoronUsers/tree/master/printer_mods/jeoje/Sturdy_Handles)
- LED strip lighting - [stuck to bars](https://www.thingiverse.com/thing:4933314/files)
- With [cable cover for top end of Z belts](https://github.com/VoronDesign/VoronUsers/tree/master/printer_mods/samwiseg0/corner_cable_hide) or [this better one](https://github.com/VoronDesign/VoronUsers/blob/ad3b6e1f34209fbf31f515cbb76d94880a948f3c/printer_mods/Dr-Info/corner_cable_cover_with_drop_down_holes/README.md)
- [Cable cover for the bottom of the z belt](https://github.com/VoronDesign/VoronUsers/tree/master/printer_mods/Akio/cable_routing_z_belt_cover) or https://www.printables.com/model/84736-z-belt-cover-a-for-voron-24
- [Deck support clips](https://github.com/VoronDesign/Voron-2/blob/Voron2.4/STLs/Panel_Mounting/deck_support_4mm_x8.stl)
- [Rear chamber camera mount](https://www.thingiverse.com/thing:4756566) with [DFRobot USB 1080p camera](https://core-electronics.com.au/raspberry-pi-wide-angle-camera-module-seeed-studio.html)
- [Front top camera](https://core-electronics.com.au/lattepanda-5mp-uvc-camera.html) and [mount](https://github.com/VoronDesign/VoronUsers/tree/master/printer_mods/chri.kai.in/Angry_CAM_USB)
- [Front top camera mount](https://github.com/VoronDesign/VoronUsers/tree/master/printer_mods/chri.kai.in/Angry_CAM_USB) for a slimline [USB Camera](https://core-electronics.com.au/lattepanda-5mp-uvc-camera.html) because having to of the same cameras causes a conflict on the Raspberry Pi and only one is ever found
- Frame thermistor (bare 3950) for doing thermal expansion compensation - mounted rear left, tucked inside the rail and held in with insulating foam so that it gives a good reading of the actual frame and not the (hotter) chamber
- [BTT Smart Filament Sensor](https://biqu.equipment/products/btt-sfs-v1-0-smart-filament-sensor-detection-stuck-blocking-filament-module) and [mount](https://github.com/VoronDesign/VoronUsers/tree/master/printer_mods/Empusas/BTT_Filament_Motion_Sensor_Mount) since the run-out sensor currently does not detect jams, which didn't work out well
- [Side entry for filament](https://github.com/VoronDesign/VoronUsers/tree/master/printer_mods/120decibell/exhaust_housing_side_entry) which makes for a much better path paird with the BTT smart filament sensor, above
- Then some nice clips to hold down the cables [here](https://www.printables.com/model/118550-cable-clip-for-2020-extrusion/files), [here](https://github.com/VoronDesign/VoronUsers/tree/master/printer_mods/evandepol/Voron2.4-Cable-clamps) and [here](https://www.printables.com/en/model/203062-ender-3-2020-extrusion-zip-tie-clips-imported-from/files)
- [Exhaust grill with notched exit for ease of cable entry](https://www.printables.com/model/366499-voron-24-canbus-umbilical/files)
  
## Print bed
- [Purge bucket and brush](https://github.com/VoronDesign/VoronUsers/tree/master/printer_mods/edwardyeeks/Decontaminator_Purge_Bucket_&_Nozzle_Scrubber) but also print the individual sheetstop and it is easy to get your magnetic print plate in the right place every time
- [A new purge bucket](https://www.printables.com/model/465418-purge-bucket-with-editable-size-and-tilt-angle/files)
- [Mount for the Bamboo Labs silicone brush](https://www.printables.com/model/786705-voron-24-nozzle-brush-using-bambu-labs-a1-silicone) 
- [Heating bed insulation](https://www.carbuilders.com.au/peel-stick-heat-shield)
- Rear under bed temperature sensor near the edge to better approximate when the bed had equilibrated (15C less at the edge underneath than from the sensor centrally under the heater pad)

## Undercarriage
- [Matching skirts with power inlet and filter from Trident design](https://github.com/VoronDesign/VoronUsers/tree/master/printer_mods/edwardyeeks/Tridentified_V2.4_Power_Inlet)
- [Raspberry Pi cooling fan](https://core-electronics.com.au/pimoroni-fan-shim-for-raspberry-pi.html)
- [Improved Raspberry Pi mount](https://github.com/MotorDynamicsLab/LDOVoron2/blob/main/STLs/beefy_raspberry_bracket.stl), needs extra [DIN mount](https://github.com/VoronDesign/Voron-2/blob/Voron2.4/STLs/Electronics_Bay/pcb_din_clip_x3.stl)
- CanBUS adaptor on the Raspberry Pi as described in the section on the [Umbilical Conversion](/articles/Umbilical_conversion.md)
- [Notched rear skirt for cable entry](https://www.printables.com/model/463756-voron-24r2-300mm-back-center-skirt-with-cable-hole/files)

## Software
- Start with [MainSail OS](https://docs-os.mainsail.xyz/), which includes all the main software components like Mainsail, Klipper, Moonraker, Crowsnest, Sonar, [Timelapse](https://github.com/mainsail-crew/moonraker-timelapse) and preinstalls [CanBoot](https://github.com/Arksine/CanBoot)
- [Github autocommit](https://docs.vorondesign.com/community/howto/EricZimmerman/BackupConfigToGithub.html) to backup the config to GitHub from MainSail
- [Moonraker Telegram integration](https://github.com/Raabi91/moonraker-telegram) to send message to and from the printer and get status updates
- 
- lcd_tweaks.cfg
- Change color of Stealthburner and Main [leds](https://github.com/MapleLeafMakers/KlipperMacros) to show extruder and bed temperature
- Fan control for Octopus - temperature controlled
- Fan control for exhaust fan - keeps more stable chamber temp
- Z-axis frame thermal expansion compensation - now built into Klipper

- [Klipper adaptive meshing and purging](https://github.com/kyleisah/Klipper-Adaptive-Meshing-Purging) which improved single part printing and also replaced my home grown fuzzy purge line and purge bucket macros

## [Klipper updating on the MCUs](https://github.com/IconoclastXYZ/Voron/blob/main/articles/klipper_updates.md)

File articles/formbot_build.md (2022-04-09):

# FORMBOT 3D Suggestions and Learning Points

## A few things I noticed during the build
- M3 x 12mm SHCS - short 4 - current spec and even 2.4r1 requires more than supplied
- M5 x 40mm SHCS - couple with unfinished heads, but enough spares
- Z axis Gates belts - spec says they should be longer than you supplied, and they are too short to easily tie up at their ends. Only needs another 5cm each
- 3M UHB tape is not in fact high bond
- Chamber base plate (black plastic) is ~2mm oversized to the supplied frame and to the spec
- SSR connector wires were terminated incorrectly for the Octopus board
- Hotend E motor wire was short - only just made it
- Combined 240v socket and switch is pressfit, but does not fit the printed parts, which were to spec
 
## A few improvements that could be made to the kit
### Tell people EXACTLY what is supplied
- Hall effect sensor board and wiring are supplied for the X & Y stops - this changes the printed parts required
- Z endstop board and wiring is supplied - this changes the printed parts required
- Hotend thermistor - specify the type / model, needed when setting up Klipper
- Heater bed thermistor - specify the type  model, needed when setting up klipper
- Inductive probe - specify modela and whether NO or NC is supplied, needed when setting up Klipper
- What type of 240v socket/switch is supplied
 
### Some inclusion that would be great, or things to do yourself
- Blue Locktite or equivalent
- GND bridging wire to get common ground for the 24v and 5v PSUs
- Separate 240v socket and switch, as now recommended
- Z end stop pin WITH the flat ground in it so it can be retained with a grub screw

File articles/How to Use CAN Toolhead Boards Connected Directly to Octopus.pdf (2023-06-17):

How to Use CAN Toolhead Boards Connected Directly to Octopus / Octopus Pro on CanBoot

- Klipper has a new CAN bus feature, the USB to CAN bus bridge communication for Octopus boards (and other compatible MCUs).
- This feature allows the Octopus boards (and other compatible MCUs) to act as a USB to CAN bus adapter. This replaces the need for an adapter like a Raspberry Pi CAN HAT, canable adapter, or the Bigtreetech U2C board.

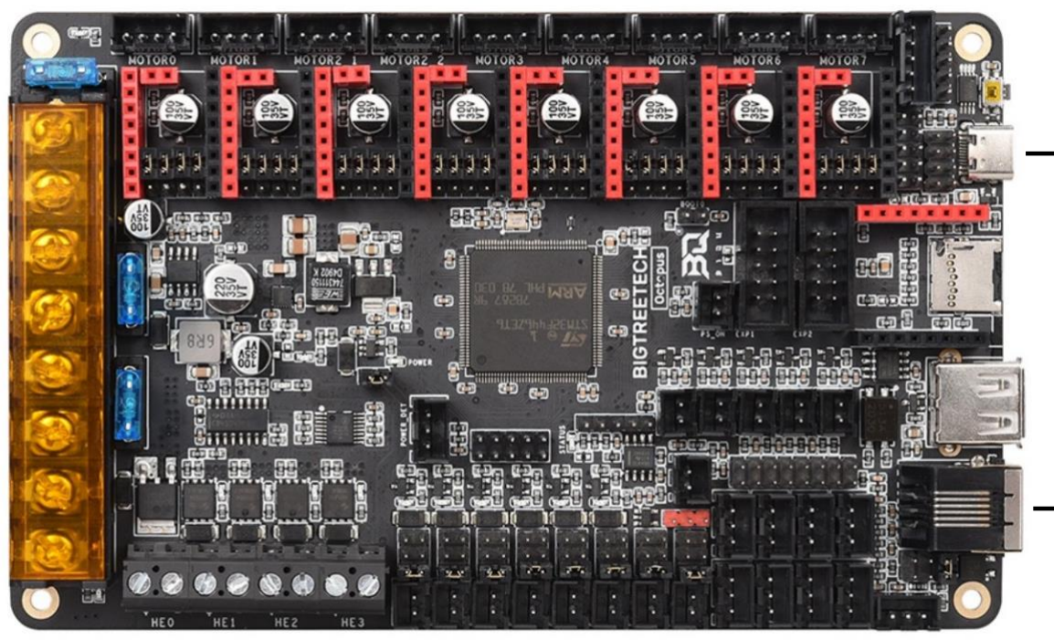
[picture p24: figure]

What is CanBoot?

- CanBoot is a custom bootloader loaded onto your Octopus and EBB board that allows users to update Klipper firmware over USB, UART, or CAN comms without physically having to access the board reset buttons or BOOT jumpers.
- It uses the same ‘make menuconfig’ setup to configure and compile firmware.
- CanBoot is NOT required to use the Klipper USB to CAN bus bridge comms. But I have not tested this comms feature separately.

You Will Need the Following

- USB-A to USB-C cable
- Power supply for Octopus and EBB toolboard (i.e. printer)
- RJ11 or RJ12 telephone cable, crimped to connect EBB board to Octopus
- See wiring info at end of guide. Best to setup wiring before installing software.
- Raspberry Pi, or similar, with Klipper / Moonraker / UI installed and working
- Computer with following software:
- SSH terminal software, I use PuTTY or Windows CMD
- WinSCP, to transfer files between Raspberry Pi and computer
- I also use Windows CMD to do this
- STM32CubeProgrammer
- Download for your computer OS and install
- https://www.st.com/en/development-tools/stm32cubeprog.html#get-software (https://www.st.com/en/development-tools/stm32cubeprog.html%23get-software)

High Level Instructions, for Understanding

1. Install CanBoot on Raspberry Pi, flash firmware to boards
a. Configure and compile CanBoot firmware for Octopus / Pro and EBB
b. Flash CanBoot to boards using STM32CubeProgrammer and computer
2. Setup boards for Klipper
a. Octopus - Setup Klipper for USB to CAN bus bridge, with CAN comms to EBB
b. EBB - Setup Klipper for CAN comms
c. Find serial device for Octopus / Pro on Raspberry Pi
d. Flash Klipper to Octopus / Pro with CanBoot serial command
3. Setup can0 network on Raspberry Pi, power cycle printer
4. Find CAN uuid for Boards
a. Connect EBB to Octopus / Pro, power cycle printer
5. Flash Klipper to EBB board with CanBoot CAN command
6. Printer Config Update and General Tips
7. How to Use CanBoot to update boards, Tips

Okay, enough talking! Let’s get started!

Instructions________________________________________________________________________

1. Install CanBoot on Raspberry Pi, flash firmware to boards

Start your SSH terminal.

sudo apt-get install git -y #Do this if you haven’t installed git yet…

git clone https://github.com/Arksine/CanBoot

cd CanBoot

make menuconfig

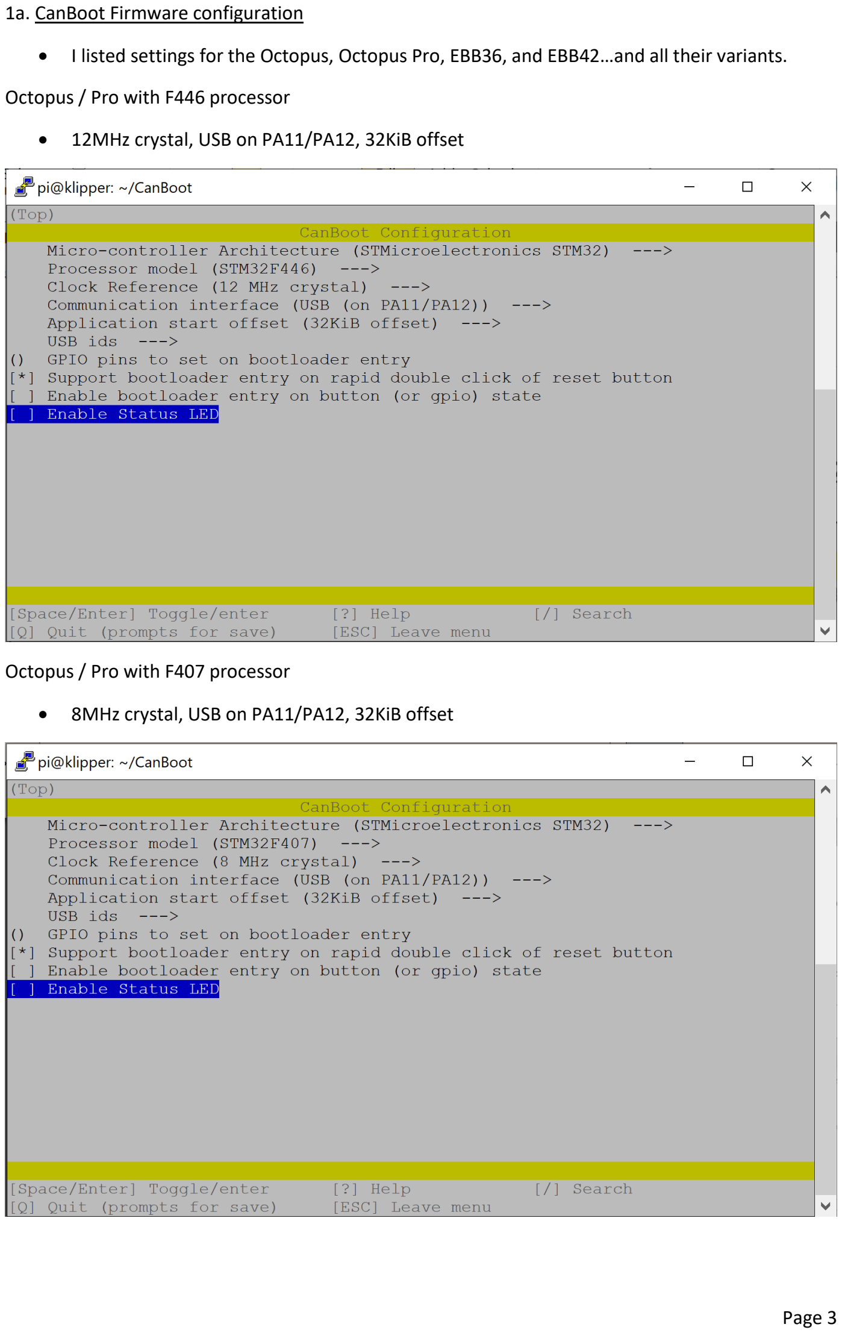
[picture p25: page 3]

1a. CanBoot Firmware configuration

- I listed settings for the Octopus, Octopus Pro, EBB36, and EBB42…and all their variants.

Octopus / Pro with F446 processor

- 12MHz crystal, USB on PA11/PA12, 32KiB offset

Octopus / Pro with F407 processor

- 8MHz crystal, USB on PA11/PA12, 32KiB offset

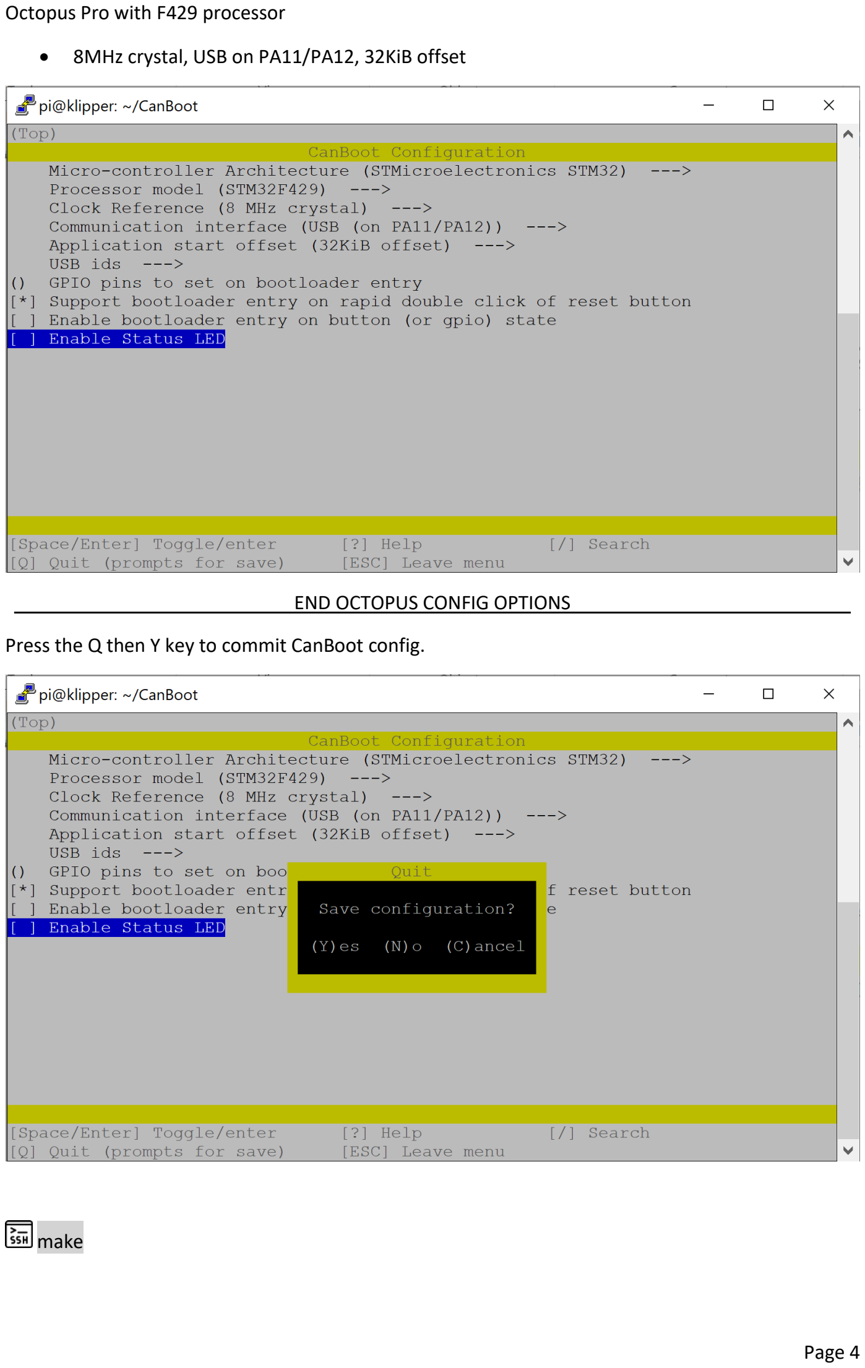
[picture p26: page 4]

Octopus Pro with F429 processor

- 8MHz crystal, USB on PA11/PA12, 32KiB offset

___________________________END OCTOPUS CONFIG OPTIONS___________________________

Press the Q then Y key to commit CanBoot config.

make

You have now created a canboot.bin firmware file for your Octopus board. My approach is to now make the CanBoot firmware for the EBB board. But if you do this now it will override the Octopus firmware you just created. So do the following:

On your computer, open a Windows CMD terminal

Type: pscp -C pi@<IP_ADDRESS>:/home/pi/CanBoot/out/canboot.bin octopus_canboot.bin

- Make sure to replace <IP_ADDRESS> with your Pi IP address or network name, like fluiddpi.local

NOTE: You can also manually move the canboot.bin file to your computer with WinSCP. Make sure to name it octopus_canboot.bin (or similar). We will be moving an ebb_canboot.bin file next.

…Back to the Raspberry Pi SSH terminal

make clean

make menuconfig

EBB36 / EBB42 v1.0 with F072 processor

- 8MHz crystal, CAN bus on PB8/PB9, 8KiB offset, 500000 CAN bus speed

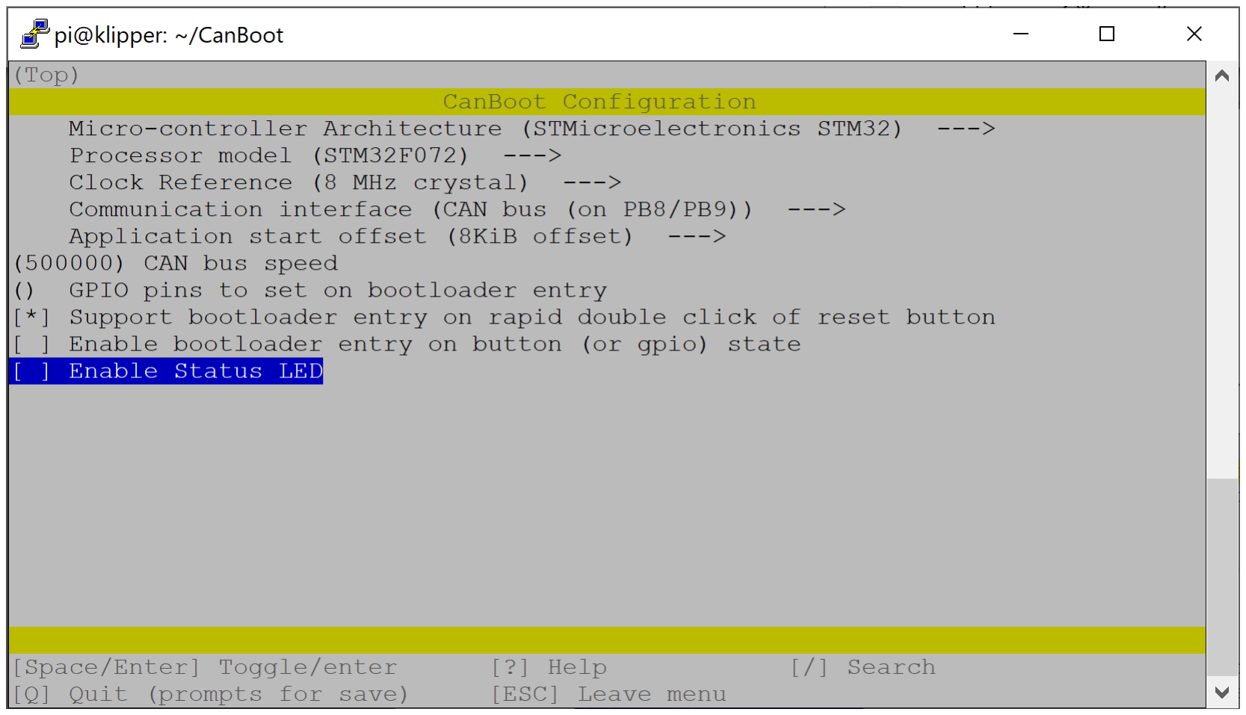
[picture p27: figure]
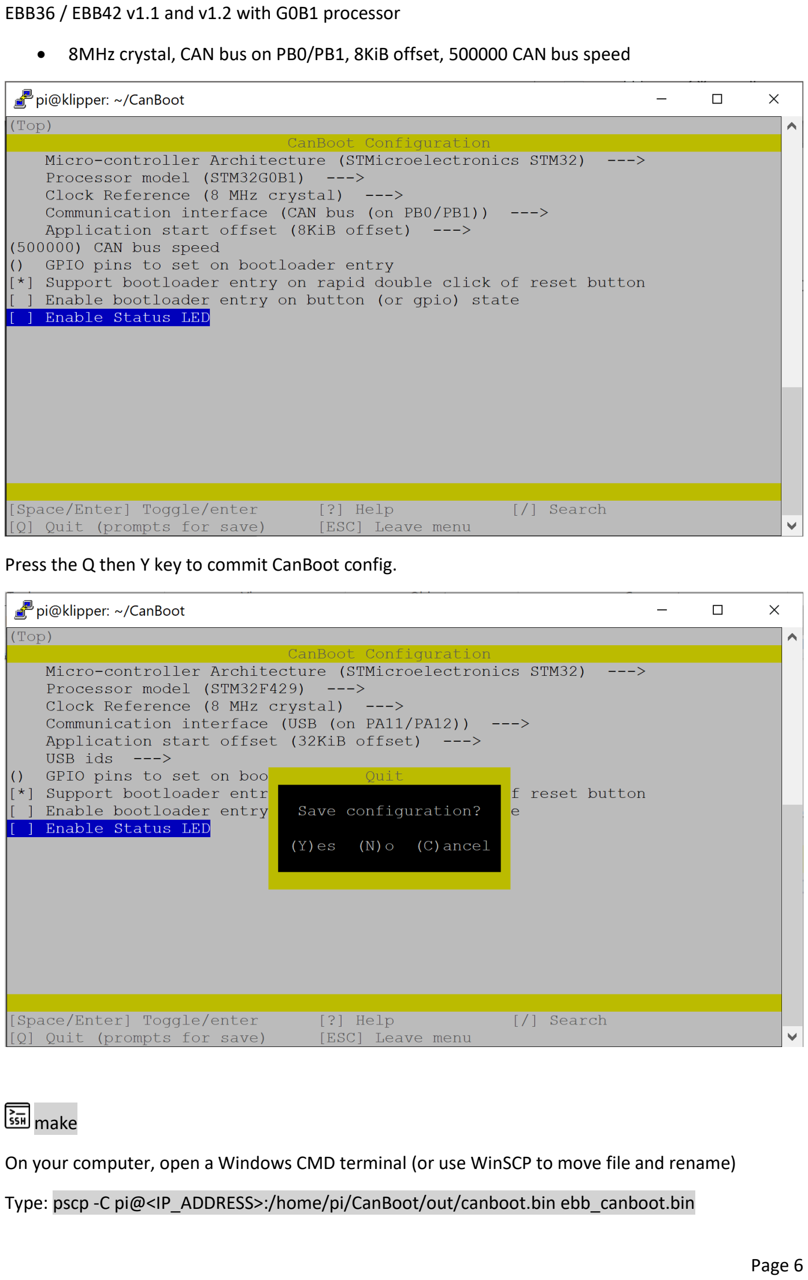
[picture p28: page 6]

EBB36 / EBB42 v1.1 and v1.2 with G0B1 processor

- 8MHz crystal, CAN bus on PB0/PB1, 8KiB offset, 500000 CAN bus speed

Press the Q then Y key to commit CanBoot config.

make

On your computer, open a Windows CMD terminal (or use WinSCP to move file and rename)

Type: pscp -C pi@<IP_ADDRESS>:/home/pi/CanBoot/out/canboot.bin ebb_canboot.bin

- Make sure to replace <IP_ADDRESS> with your Pi IP address or network name, like fluiddpi.local

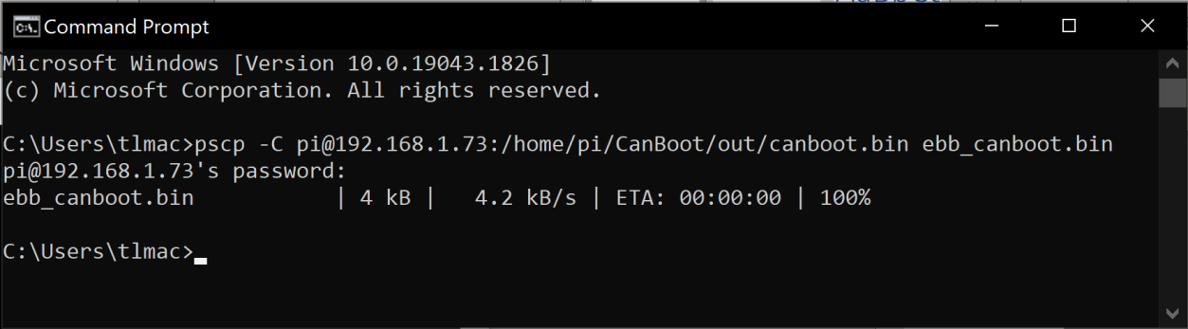
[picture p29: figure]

Your two CanBoot firmware files are now on your computer (in your user folder). Next step is to flash CanBoot to your boards.

1b. Flash CanBoot using STM32CubeProgrammer

You’ll need to put your boards into DFU mode and connect to the computer using a USB-A to USB-C cable. Boot instructions for the Octopus and Octopus Pro are below:

Make sure the power is off to the Octopus board

- To start have the USB-C to USB-A cable connected between the Windows PC and the Octopus Board.
- Remove the USB-C power jumper and place a jumper on the Boot0 header.

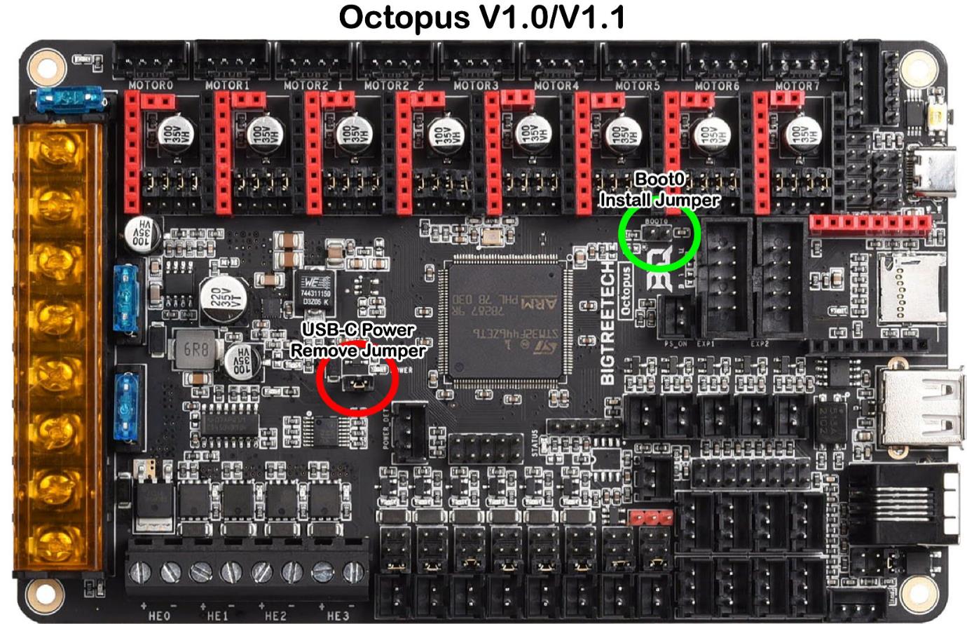
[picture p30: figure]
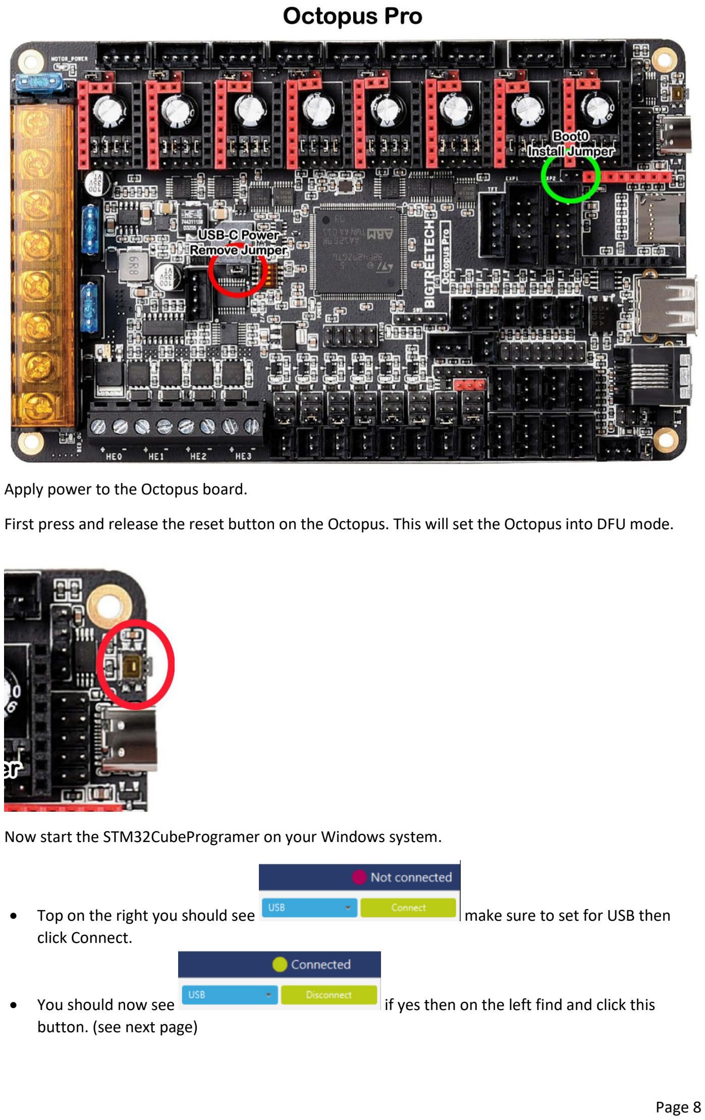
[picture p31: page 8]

Apply power to the Octopus board.

First press and release the reset button on the Octopus. This will set the Octopus into DFU mode.

Now start the STM32CubeProgramer on your Windows system.

- | Top on the right you should see | make sure to set for USB then
| click Connect.
- | You should now see | if yes then on the left find and click this
| button. (see next page)

- For CanBoot and Klipper to work correctly we need to wipe the flash memory by clicking this button.

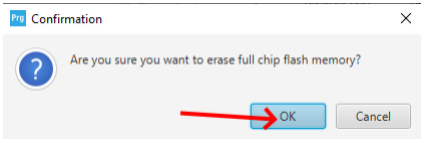
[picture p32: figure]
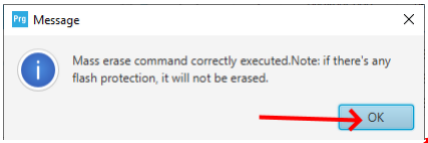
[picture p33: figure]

- Go back to main page by clicking on this button

- Select (1) “Open File” tab, find the octopus_canboot.bin file, and (2) download to your Octopus board. (3) Click Disconnect when done.

Power off your Octopus board. Remove the jumper from BOOT0.

Now you’ll flash your EBB toolboard.

This step will power the toolboard from USB only. Place a jumper on VBUS header.

EBB36 / EBB42 v1.0

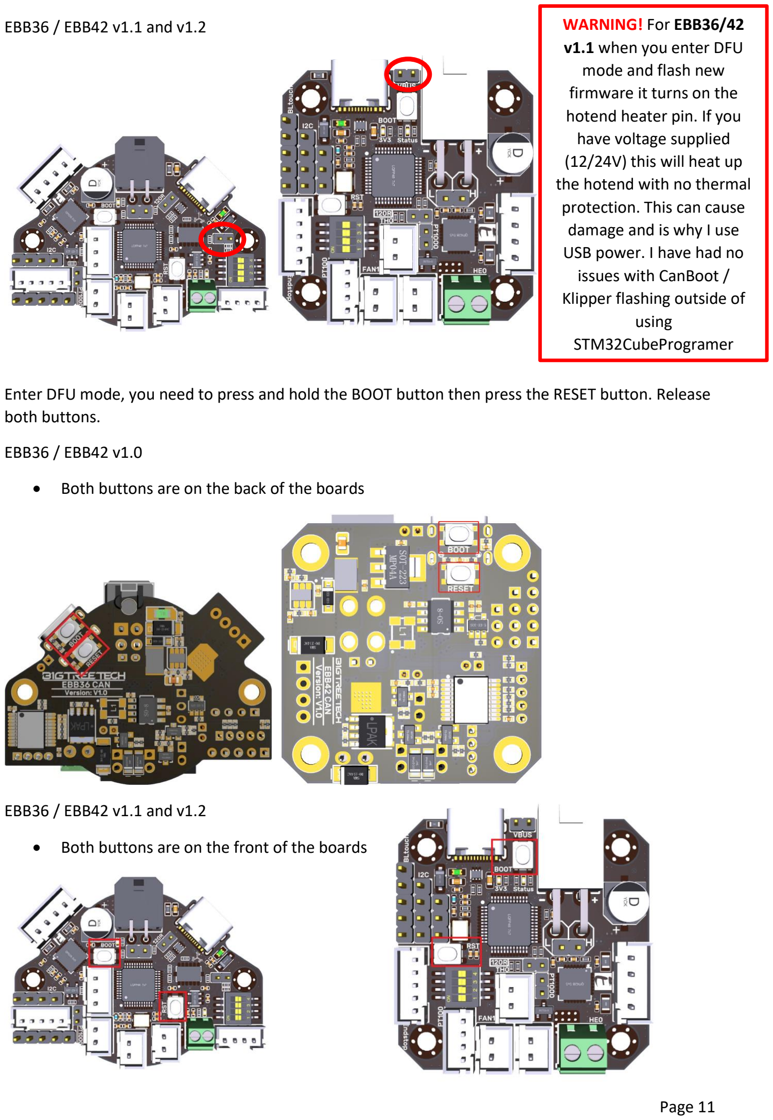
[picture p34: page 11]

EBB36 / EBB42 v1.1 and v1.2

Enter DFU mode, you need to press and hold the BOOT button then press the RESET button. Release both buttons.

EBB36 / EBB42 v1.0

- Both buttons are on the back of the boards

EBB36 / EBB42 v1.1 and v1.2

- Both buttons are on the front of the boards

WARNING! For EBB36/42
v1.1 when you enter DFU
mode and flash new
firmware it turns on the
hotend heater pin. If you
have voltage supplied
(12/24V) this will heat up the hotend with no thermal protection. This can cause damage and is why I use
USB power. I have had no
issues with CanBoot /
Klipper flashing outside of using
STM32CubeProgramer

Now start the STM32CubeProgramer on your Windows system.

- | Top on the right you should see | make sure to set for USB then
| click Connect.
- | You should now see | if yes then on the left find and click this
| button.
- For CanBoot and Klipper to work correctly we need to wipe the flash memory by clicking this button.

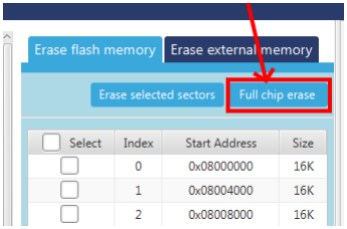
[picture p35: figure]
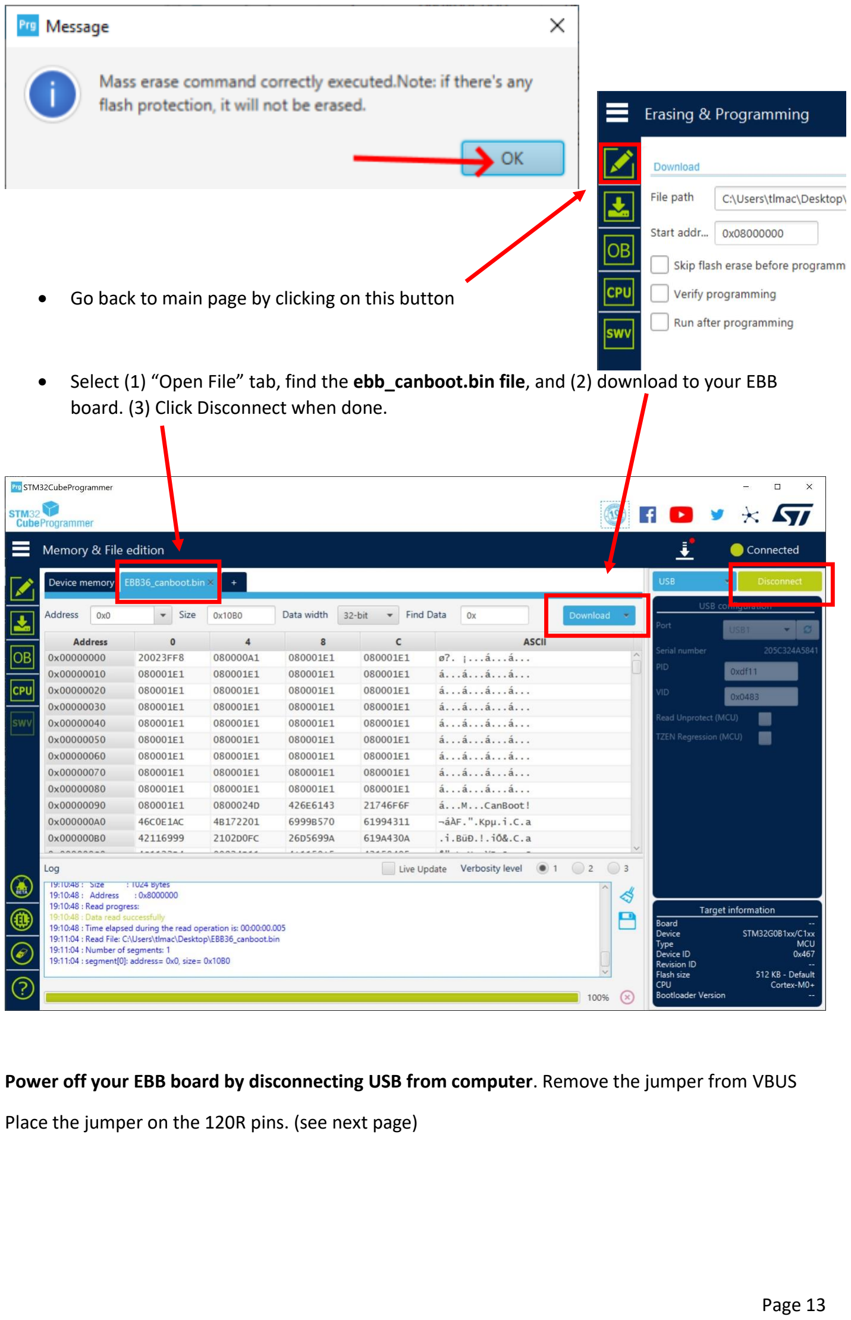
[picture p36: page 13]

- Go back to main page by clicking on this button
- Select (1) “Open File” tab, find the ebb_canboot.bin file, and (2) download to your EBB board. (3) Click Disconnect when done.

Power off your EBB board by disconnecting USB from computer. Remove the jumper from VBUS

Place the jumper on the 120R pins. (see next page)

EBB36 / EBB42 v1.0

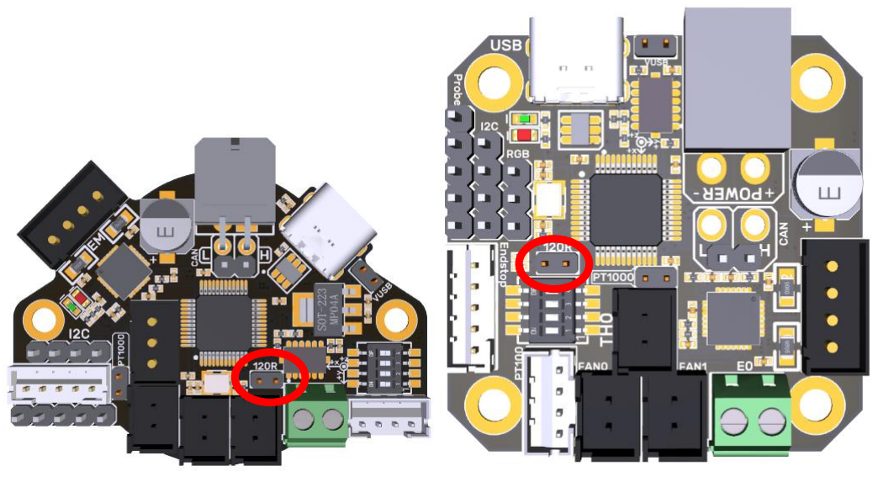
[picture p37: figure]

EBB36 / EBB42 v1.1 and v1.2

Set aside the EBB toolboard for now.

2. Setup Octopus / Pro for Klipper

Go back to your SSH terminal window.

cd ~/klipper

make menuconfig

2a. Octopus - Setup Klipper for USB to CAN bus bridge, with CAN comms to EBB

You will now setup the new USB to CAN bus bridge on your Octopus / Pro board. Below are the Klipper config options for each board. Make sure to have “Enable extra low-level configuration options” selected.

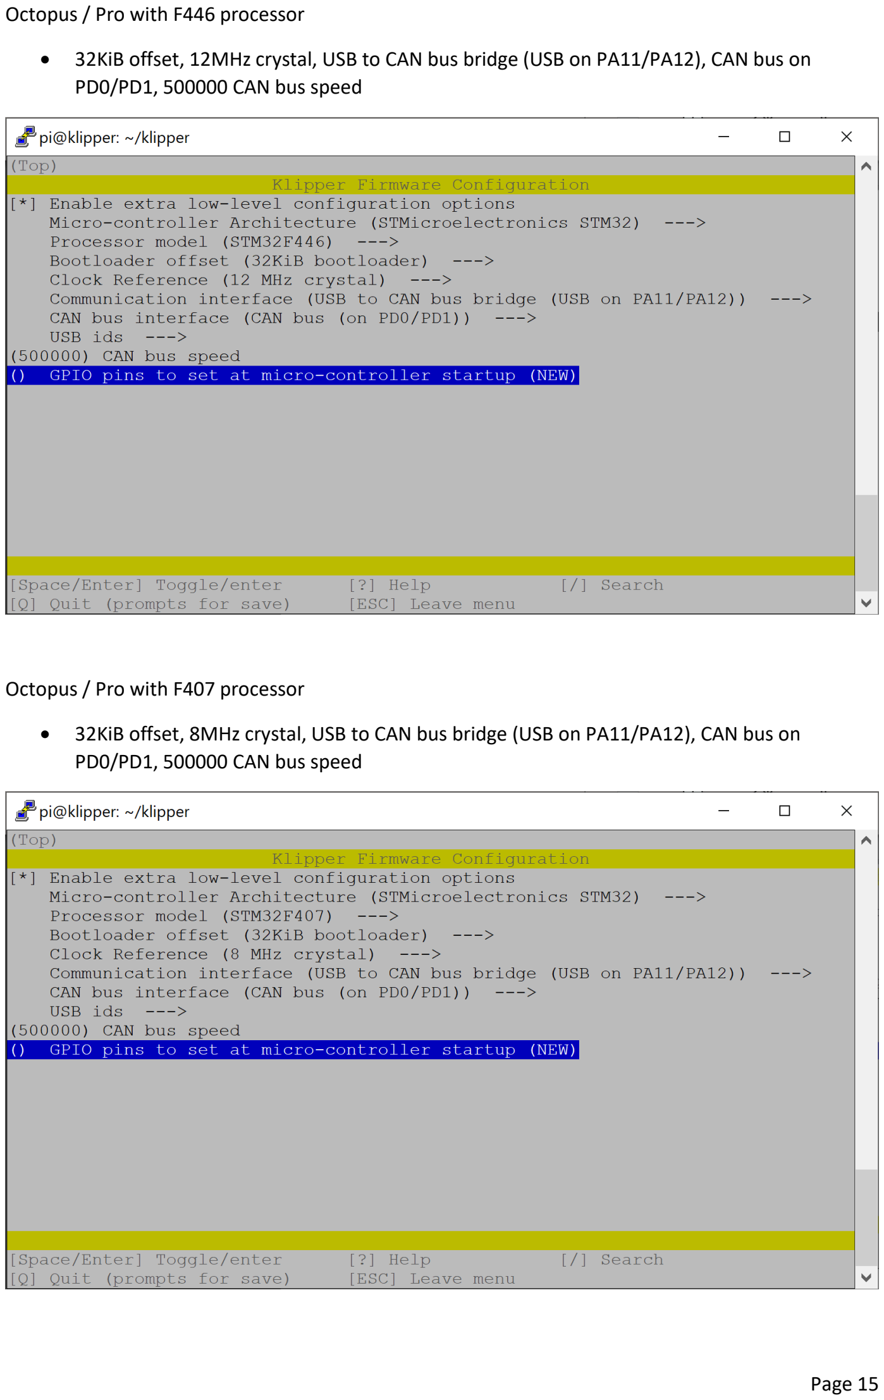
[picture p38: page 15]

Octopus / Pro with F446 processor

- 32KiB offset, 12MHz crystal, USB to CAN bus bridge (USB on PA11/PA12), CAN bus on PD0/PD1, 500000 CAN bus speed

Octopus / Pro with F407 processor

- 32KiB offset, 8MHz crystal, USB to CAN bus bridge (USB on PA11/PA12), CAN bus on PD0/PD1, 500000 CAN bus speed

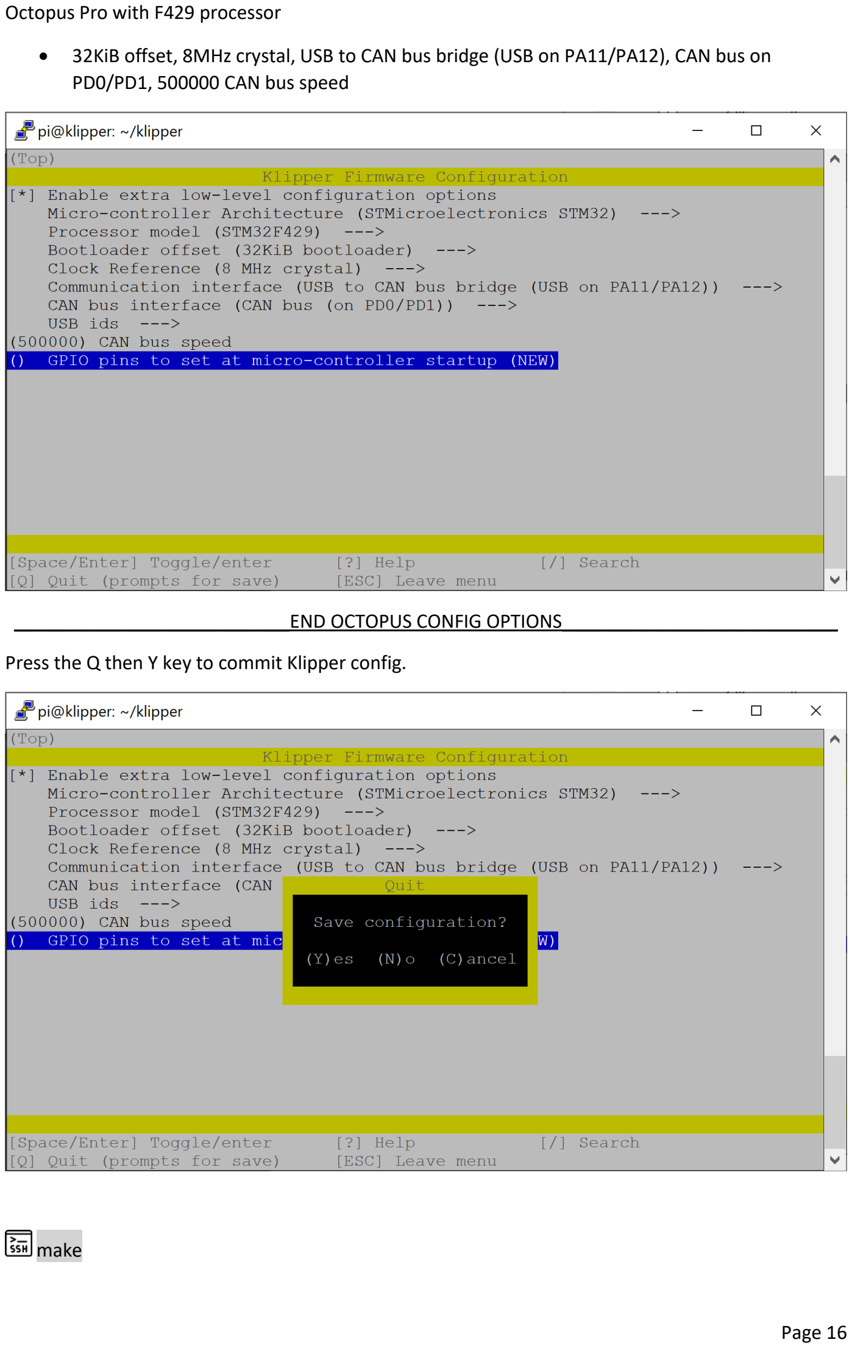
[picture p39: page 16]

Octopus Pro with F429 processor

- 32KiB offset, 8MHz crystal, USB to CAN bus bridge (USB on PA11/PA12), CAN bus on PD0/PD1, 500000 CAN bus speed

___________________________END OCTOPUS CONFIG OPTIONS___________________________

Press the Q then Y key to commit Klipper config.

make

NOTE:

Just like with the CanBoot firmware we will be making Klipper firmware for the Octopus / Pro board and the EBB board. Since we are already compiling Klipper firmware, I like to compile the EBB Klipper firmware now. But if we do, then the Octopus Klipper firmware we just made will be overwritten. So:

mv ~/klipper/out/klipper.bin octopus_klipper.bin

make clean

NOTE:

This moves the klipper firmware file to the klipper folder and renames it octopus_klipper.bin then deletes the compile files and folders, including /klipper/out

2b. EBB - Setup Klipper for CAN comms

make menuconfig

EBB36 / EBB42 v1.0 with F072 processor

- 8KiB bootloader, 8MHz crystal, CAN bus on PB8/PB9, 500000 CAN bus speed

EBB36 / EBB42 v1.1 / v1.2 with G0B1 processor

- 8KiB bootloader, 8MHz crystal, CAN bus on PB0/PB1, 500000 CAN bus speed

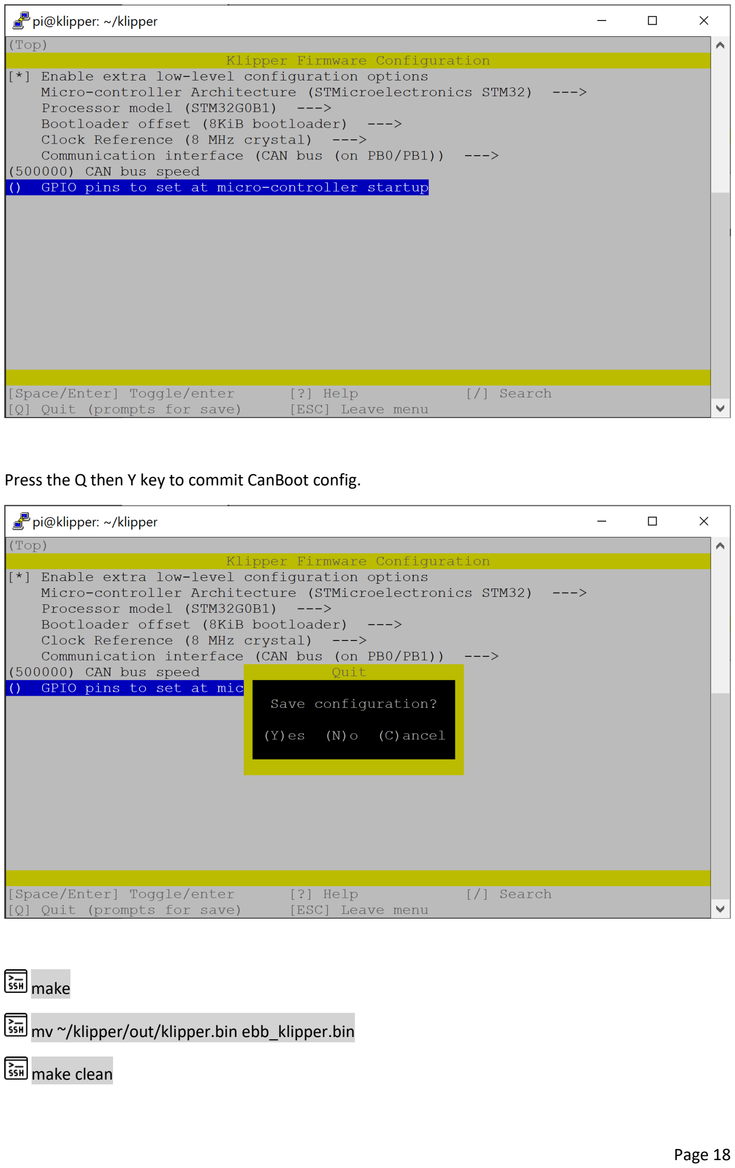
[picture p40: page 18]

Press the Q then Y key to commit CanBoot config.

make

mv ~/klipper/out/klipper.bin ebb_klipper.bin

make clean

2c. Find serial device for Octopus / Pro on Raspberry Pi

Connect your Octopus / Pro board to the Raspberry Pi with a USB-A to USB-C cable…connected to the USB-C port on the Octopus board. Power on your printer.

cd

ls /dev/serial/by-id/*

This will give you something similar to below. YOUR DEVICE WILL BE DIFFERENT!

Copy this, for example:

/dev/serial/by-id/usb-CanBoot_stm32f429xx_350026000B50314B33323220-if00

2d. Flash Klipper to Octopus / Pro with CanBoot serial command

cd CanBoot/scripts

pip3 install pyserial

…this only has to be done once

python3 flash_can.py -f ~/klipper/octopus_klipper.bin -d <serial_device>

NOTE: Replace <serial_device> with the path you copied earlier…

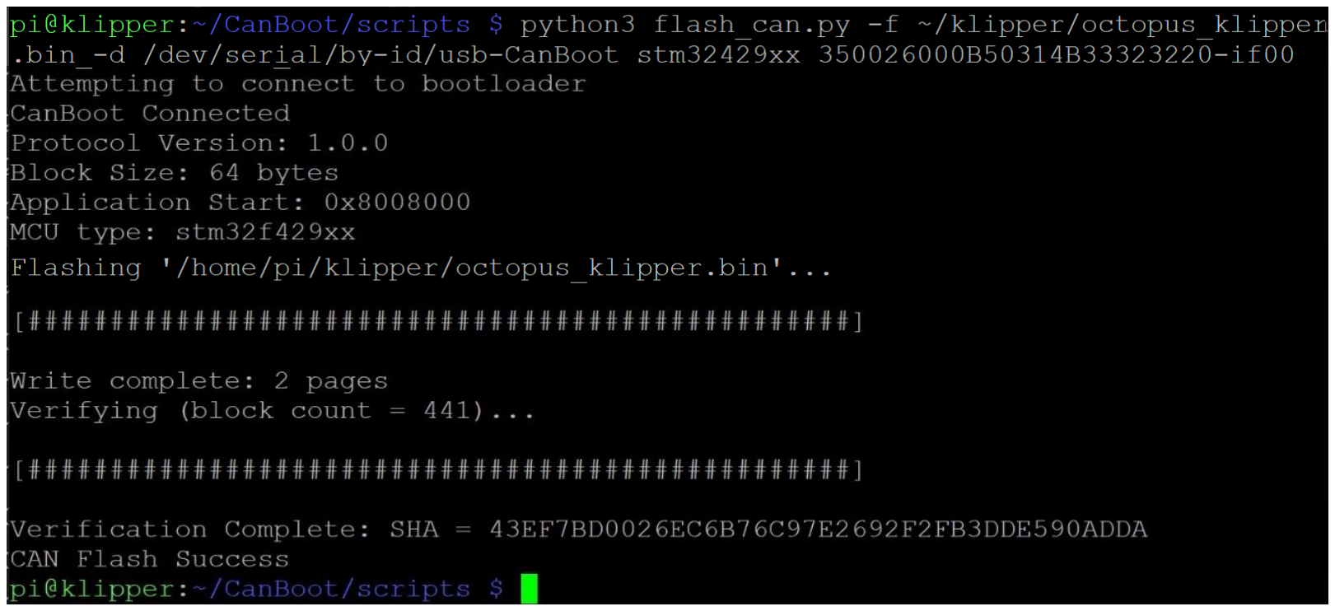
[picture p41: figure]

NOTE: The Octopus board communicates over USB initially. Only this flash (and Klipper updates, more on that later) use the serial device path. The Octopus board now has a CAN uuid…let’s find it!

3. Setup can0 Network on Raspberry Pi, Power Cycle Printer

Now we need to enable the can0 network and set it up so that we can have CAN bus working

cd

sudo nano /etc/network/interfaces.d/can0

- Copy and paste the following:

allow-hotplug can0
iface can0 can static
bitrate 500000
up ifconfig $IFACE txqueuelen 128

Ctrl – X to EXIT.

Key Y for YES, and ENTER.

Power off your printer. Time to plug in your EBB toolboard. Plug power and can data cables into EBB. Plug RJ11 or RJ12 connector into Octopus / Pro board.

Power on your printer.

NOTE:

We just created the can0 interface as a hot-plug network. This means that when something changes to devices, or new devices are connected, the network reacts. Power cycling the printer is a change that the can0 network detects and configures the Octopus to work as a CAN device. Also, this hot-plug option seems to make “firmware_restarts” smoother.

4. Find CAN uuid for Octopus / Pro

Now that can0 is setup, let’s make sure it is up and running.

ifconfig

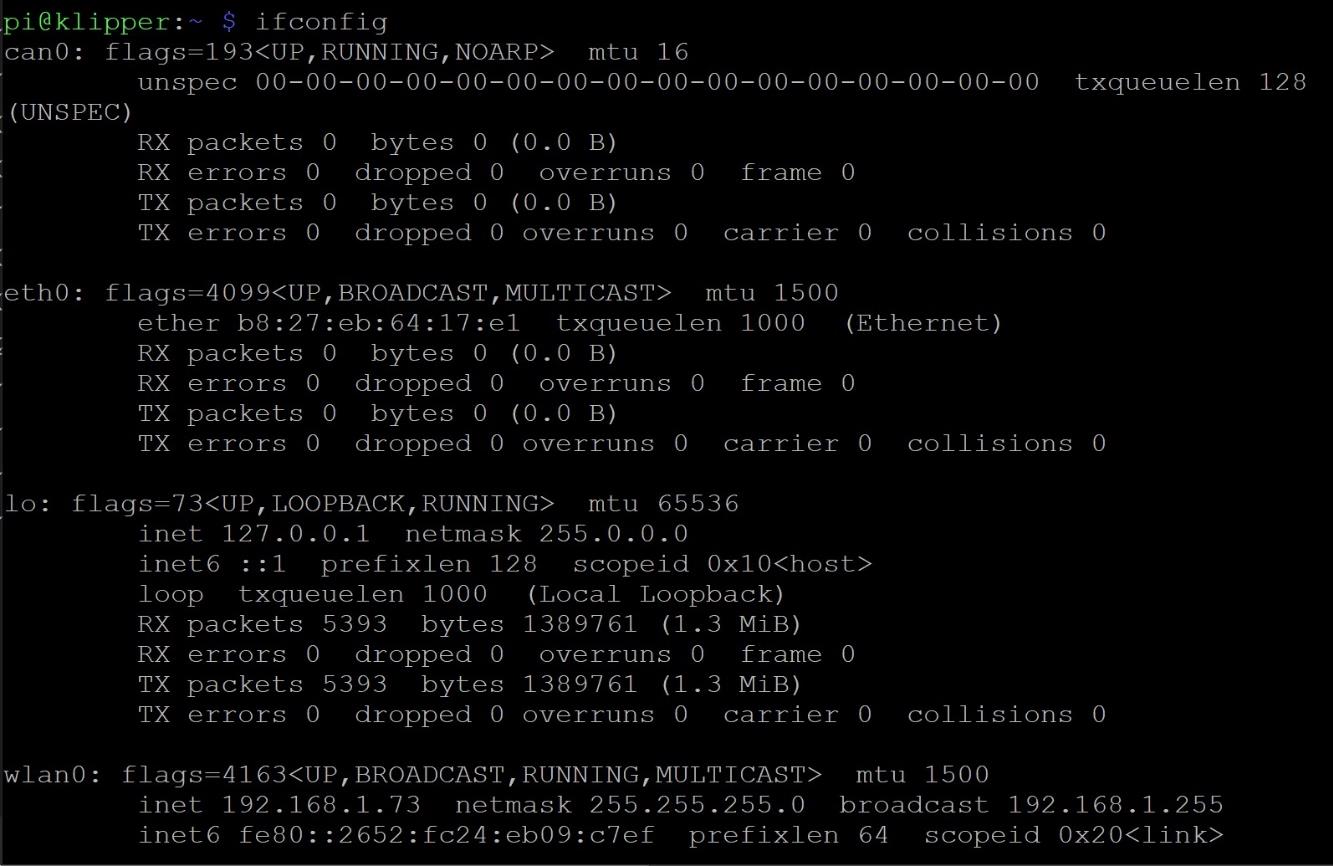
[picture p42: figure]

You should get results similar to this. We are looking for the can0 on top. Success!

NOTE: If this doesn’t work try to turn off power to your printer and reboot your Raspberry Pi. Wont booted back up, open a SSH terminal and try ifconfig again. Can0 won’t show up. Power on your printer and then try ifconfig. Should have can0 up and running.

cd CanBoot/scripts

python3 flash_can.py -i can0 -q

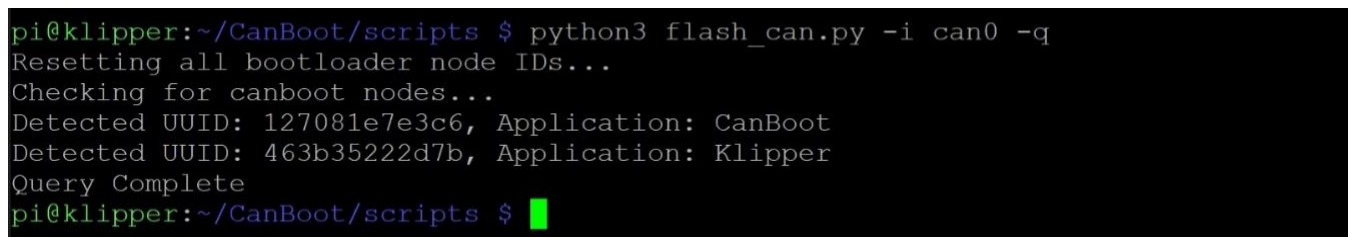
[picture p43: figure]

In this instance both EBB and Octopus are detected. The EBB only has CanBoot on it while the Octopus has Klipper. It is obvious which is which. Save both for later.

5. Flash Klipper to EBB board with CanBoot CAN command

python3 flash_can.py -f ~/klipper/ebb_klipper.bin -u <ebb_uuid>

NOTE: Replace <ebb_uuid> with the CAN uuid found before. The EBB is labelled with “CanBoot”. In this case mine is 127081e7e3c6

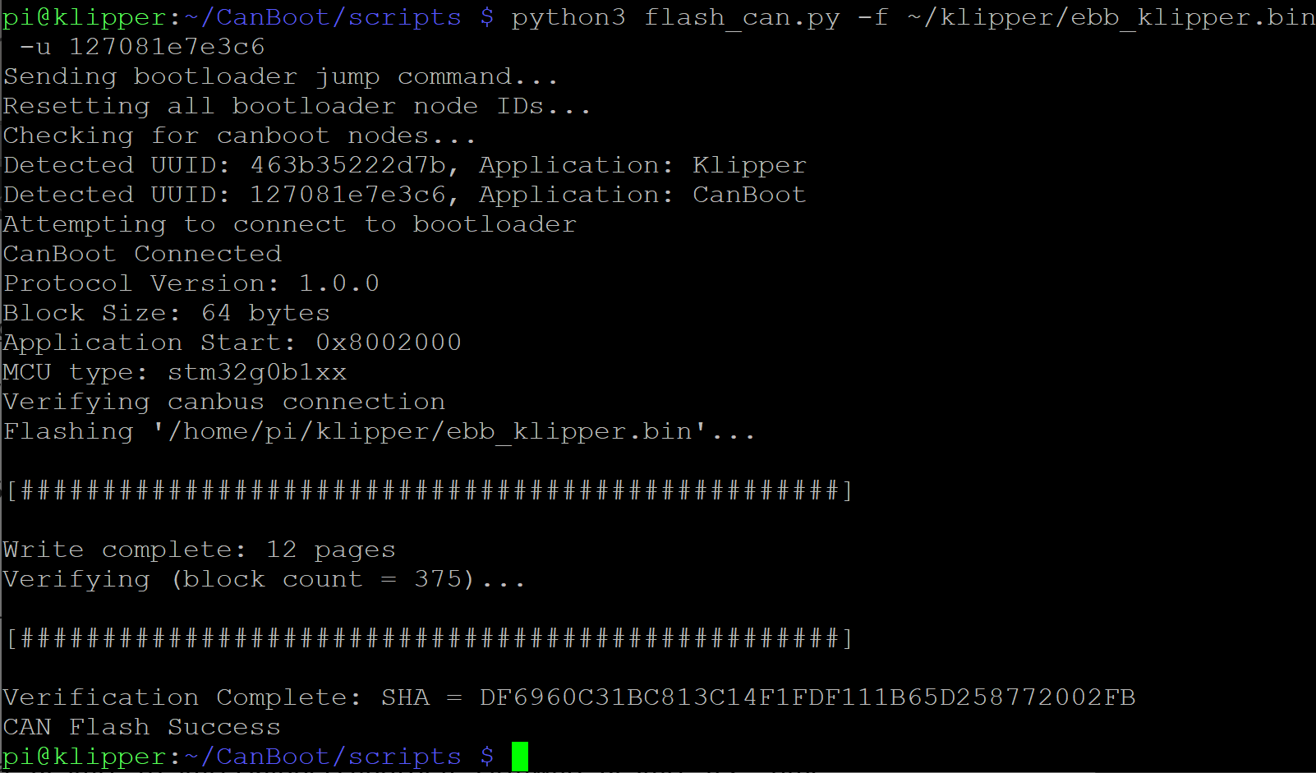
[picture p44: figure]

cd ~/klipper

rm octopus_klipper.bin ebb_klipper.bin

6. Printer Config Update and General Tips

Edit your printer.cfg to now include your new CAN uuid. For example:

[mcu]
canbus_uuid: 463b35222d7b

[mcu EBBCan]
canbus_uuid: 127081e7e3c6

Save and restart.

If you have issues here, try a “Restart” (restarts Klipper) and/or a “Firmware Restart” a 2nd time.

- The issue is can0 network disconnects when the restart causes a power cycle on your printer. The timing can be too fast and the can0 network doesn’t properly come back up. Another restart command is sometimes needed.
- | According to Klipper CANBUS docs, you might need to issue | sudo ip up in a SSH terminal to
restart the can0 network. I haven’t had to do this. But this might be useful during initial setup.

- | You can also use | sudo ip link set up can0 type can bitrate 500000 in a SSH terminal to start
can0 if it isn’t coming up with ifconfig. I have used this, but find that if the install instructions are followed then I don’t need it.
- See Klipper docs on CANBUS for official information https://www.klipper3d.org/CANBUS.html#usb-to-can-bus-bridge-mode
7. How to Use CanBoot to update boards, Tips

With CanBoot and Klipper now properly flashed to your Octopus / Pro board and EBB toolboard you now have two devices with unique CAN uuid on can0 network. But how to use CanBoot to upgrade Klipper firmware!?

When you run python3 flash_can.py | the python script should trigger the board to go into DFU
mode, to access CanBoot on the board and flash the Klipper update. I can’t cleanly get this to work with my Octopus Pro with F429 processor.
- Flashing with CAN uuid gives an error. Trying to use the original serial ID also gives an error.
- How I get it to work:
- Make Klipper firmware for Octopus board, cd to CanBoot/scripts
- I run: python3 flash_can.py -f ~/klipper/octopus_klipper.bin -u 463b35222d7b
- Note I am still moving and renaming firmware files. If you don’t want to do this then leave out: -f ~/klipper/octopus_klipper.bin and CanBoot defaults to using default location of Klipper firmware [ ~/klipper/out/klipper.bin ]
- CanBoot throws an error. If I try ifconfig, the can0 network is down
- Now if I try ls /dev/serial/by-id/* I get a serial ID:
- /dev/serial/by-id/usb-CanBoot_stm32f429xx_350026000B50314B33323220-if00
- Same as earlier…
- Now I run:
- python3 flash_can.py -f ~/klipper/octopus_klipper.bin -d /dev/serial/by-id/usb-CanBoot_stm32f429xx_350026000B50314B33323220-if00
- And CanBoot works and flashes Klipper update!
- I can now update the EBB with: python3 flash_can.py -f ~/klipper/ebb_klipper.bin -u 127081e7e3c6

Long story short;

1. Try to flash Octopus board with CAN uuid, it will fail and can0 network is down.
2. Now you can flash Octopus board with serial ID.
3. Lastly you can flash EBB board with CAN uuid.

CAN Bus Wiring on next page…

RJ11 / RJ12 CAN bus Wiring Info

To connect your EBB36/42 or other CAN enabled toolboard directly to the Octopus boards you need to use the RJ11 / RJ12 telephone port.

The easiest option is to use a 2-3 meter telephone cable and cut off one end. Crimp for Molex MiniFit or Molex MicroFit connector, depending on your CAN toolboard. The RJ11/12 connector goes to the Octopus board.

- This does not allow for twisted wire, which is recommended for CAN bus wiring.
- I have the 4 wire RJ11 telephone cable running directly to my EBB36, no twisted wire. No issues on my end but I will work to get twisted wire setup in the future.

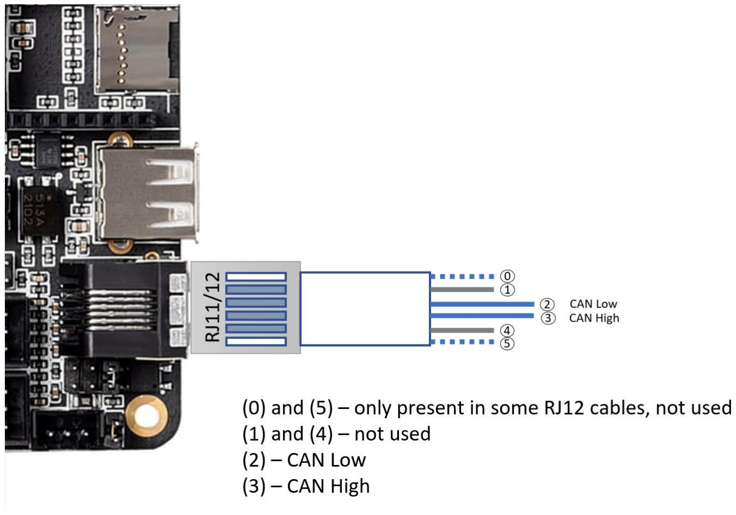
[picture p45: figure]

When you plug in the RJ11/12 cable to the Octopus board, the wiring (from top down) is as above. DO NOT RELY ON WIRE COLOURS. For example:

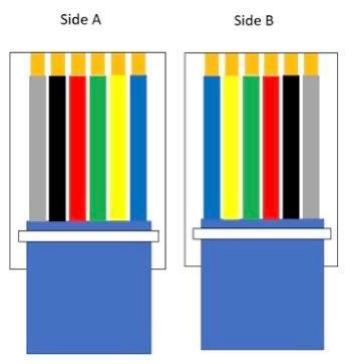
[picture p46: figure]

If plugging in a RJ12 cable with SIDE A your CAN Low wire is GREEN and CAN High wire is RED.

If plugging in a RJ12 cable with SIDE B your CAN Low wire is RED and CAN High wire is GREEN.

The colour of your wiring setup will be situational.

Take note of the wiring that you have plugged into the Octopus board. Wire 2 is your CAN Low connection. Note the colour of the wire and make sure it goes to CAN_L on the EBB end. Same thing for the CAN High on Wire 3. That colour wire goes to CAN_H on the EBB end.

You must also supply 12V or 24V directly to the EBB toolboard. Run 18awg directly from your power supply. Example EBB connections are below. Again, colours on the diagrams do not indicate wire colours.

EBB36

EBB42

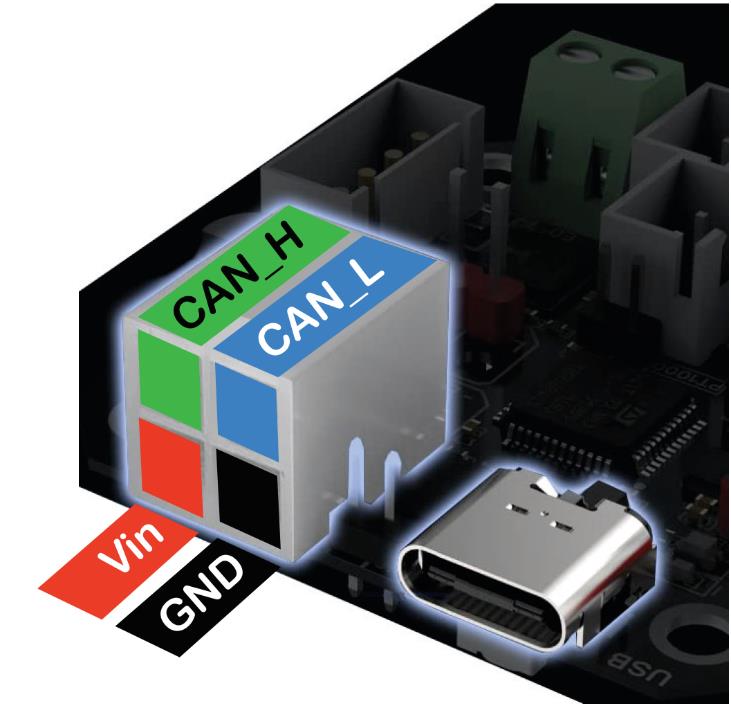
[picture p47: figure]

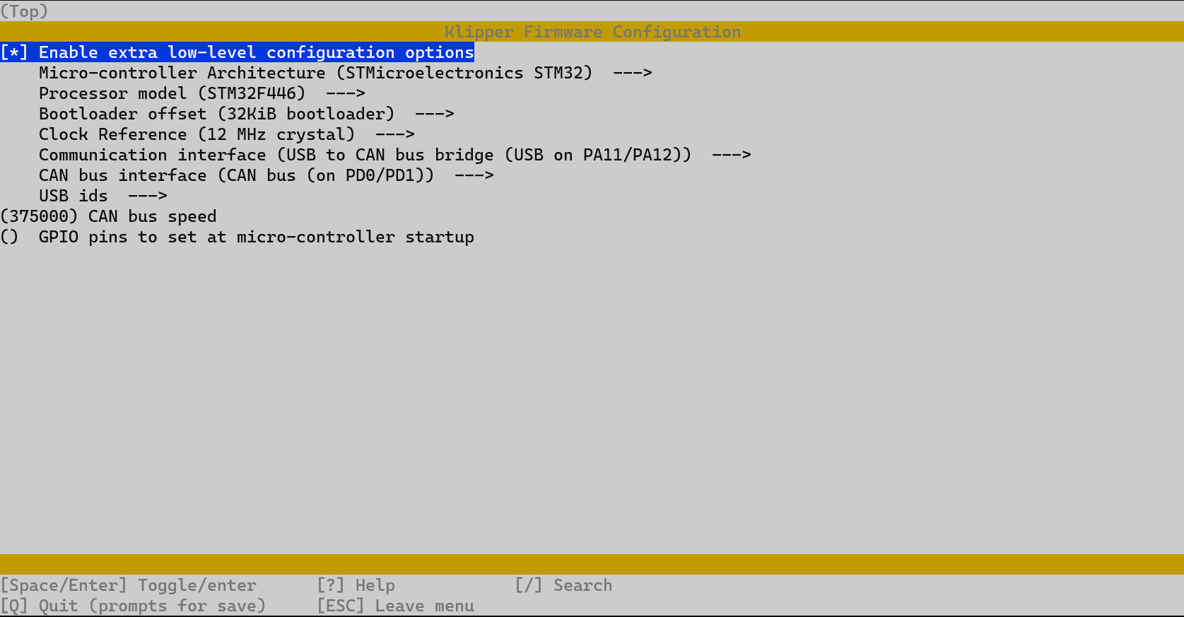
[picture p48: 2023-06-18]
images/KlipperSetup-Octopus-CanBUS.png

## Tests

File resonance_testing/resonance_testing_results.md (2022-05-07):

# Results from Resonance Testing

## 20220507
### ABBN 30 head with PA6 CF hotend and Dragon HF

~/klipper/scripts/calibrate_shaper.py /tmp/resonances_x_*.csv -o /tmp/shaper_calibrate_x.png

Fitted shaper 'zv' frequency = 57.8 Hz (vibrations = 5.4%, smoothing ~= 0.053)
To avoid too much smoothing with 'zv', suggested max_accel <= 13000 mm/sec^2

Fitted shaper 'mzv' frequency = 58.8 Hz (vibrations = 0.0%, smoothing ~= 0.059)
To avoid too much smoothing with 'mzv', suggested max_accel <= 10200 mm/sec^2

Fitted shaper 'ei' frequency = 70.2 Hz (vibrations = 0.0%, smoothing ~= 0.065)
To avoid too much smoothing with 'ei', suggested max_accel <= 9200 mm/sec^2

Fitted shaper '2hump_ei' frequency = 87.6 Hz (vibrations = 0.0%, smoothing ~= 0.070)
To avoid too much smoothing with '2hump_ei', suggested max_accel <= 8500 mm/sec^2

Fitted shaper '3hump_ei' frequency = 105.0 Hz (vibrations = 0.0%, smoothing ~= 0.074)
To avoid too much smoothing with '3hump_ei', suggested max_accel <= 8100 mm/sec^2

Recommended shaper is mzv @ 58.8 Hz

~/klipper/scripts/calibrate_shaper.py /tmp/resonances_y_*.csv -o /tmp/shaper_calibrate_y.png

Fitted shaper 'zv' frequency = 40.6 Hz (vibrations = 1.9%, smoothing ~= 0.098)
To avoid too much smoothing with 'zv', suggested max_accel <= 6400 mm/sec^2

Fitted shaper 'mzv' frequency = 40.8 Hz (vibrations = 0.0%, smoothing ~= 0.122)
To avoid too much smoothing with 'mzv', suggested max_accel <= 4900 mm/sec^2

Fitted shaper 'ei' frequency = 49.2 Hz (vibrations = 0.0%, smoothing ~= 0.133)
To avoid too much smoothing with 'ei', suggested max_accel <= 4500 mm/sec^2

Fitted shaper '2hump_ei' frequency = 61.6 Hz (vibrations = 0.0%, smoothing ~= 0.142)
To avoid too much smoothing with '2hump_ei', suggested max_accel <= 4200 mm/sec^2

Fitted shaper '3hump_ei' frequency = 74.4 Hz (vibrations = 0.0%, smoothing ~= 0.148)
To avoid too much smoothing with '3hump_ei', suggested max_accel <= 4100 mm/sec^2

Recommended shaper is mzv @ 40.8 Hz

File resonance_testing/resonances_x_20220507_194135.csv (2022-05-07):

freq | psd_x | psd_y | psd_z | psd_xyz
0.0 | 5.843e+02 | 7.932e+01 | 1.972e+01 | 6.834e+02
1.6 | 4.305e+02 | 5.238e+02 | 1.039e+02 | 1.058e+03
3.2 | 1.495e+02 | 5.899e+02 | 1.269e+02 | 8.663e+02
4.8 | 5.976e+02 | 5.357e+02 | 1.234e+02 | 1.257e+03
6.4 | 1.605e+03 | 5.267e+02 | 1.239e+02 | 2.256e+03
8.0 | 2.546e+03 | 5.171e+02 | 1.270e+02 | 3.190e+03
9.6 | 3.764e+03 | 4.748e+02 | 1.236e+02 | 4.363e+03
11.2 | 5.158e+03 | 4.215e+02 | 1.266e+02 | 5.706e+03
12.8 | 5.590e+03 | 4.542e+02 | 1.346e+02 | 6.179e+03
14.4 | 7.011e+03 | 4.547e+02 | 1.310e+02 | 7.597e+03
16.0 | 9.169e+03 | 4.677e+02 | 1.324e+02 | 9.769e+03
17.6 | 1.124e+04 | 4.895e+02 | 1.319e+02 | 1.186e+04
19.2 | 1.367e+04 | 4.780e+02 | 1.270e+02 | 1.428e+04
20.8 | 1.674e+04 | 5.157e+02 | 1.349e+02 | 1.739e+04
22.4 | 1.989e+04 | 4.963e+02 | 1.327e+02 | 2.052e+04
24.0 | 2.351e+04 | 4.269e+02 | 1.407e+02 | 2.408e+04
25.6 | 2.790e+04 | 4.768e+02 | 1.414e+02 | 2.852e+04
27.2 | 3.309e+04 | 5.586e+02 | 1.458e+02 | 3.380e+04
28.8 | 3.950e+04 | 5.366e+02 | 1.596e+02 | 4.020e+04
30.4 | 4.701e+04 | 5.734e+02 | 1.644e+02 | 4.775e+04
32.0 | 5.502e+04 | 5.899e+02 | 1.587e+02 | 5.577e+04
33.6 | 6.329e+04 | 5.739e+02 | 1.763e+02 | 6.404e+04
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

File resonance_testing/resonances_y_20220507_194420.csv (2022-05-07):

freq | psd_x | psd_y | psd_z | psd_xyz
0.0 | 1.568e+01 | 4.442e+01 | 5.121e+02 | 5.722e+02
1.6 | 5.815e+01 | 9.417e+01 | 3.710e+02 | 5.234e+02
3.2 | 6.643e+01 | 9.496e+01 | 1.441e+02 | 3.055e+02
4.8 | 6.989e+01 | 9.393e+01 | 5.517e+02 | 7.155e+02
6.4 | 7.536e+01 | 9.987e+01 | 1.584e+03 | 1.759e+03
8.0 | 9.057e+01 | 1.201e+02 | 2.872e+03 | 3.083e+03
9.6 | 8.443e+01 | 1.250e+02 | 4.225e+03 | 4.434e+03
11.2 | 7.177e+01 | 1.279e+02 | 3.504e+03 | 3.704e+03
12.8 | 7.517e+01 | 1.351e+02 | 4.857e+03 | 5.067e+03
14.4 | 8.804e+01 | 1.336e+02 | 7.486e+03 | 7.707e+03
16.0 | 9.346e+01 | 1.212e+02 | 1.028e+04 | 1.050e+04
17.6 | 1.056e+02 | 1.268e+02 | 1.328e+04 | 1.351e+04
19.2 | 1.149e+02 | 1.444e+02 | 1.693e+04 | 1.718e+04
20.8 | 1.220e+02 | 1.583e+02 | 2.141e+04 | 2.169e+04
22.4 | 1.330e+02 | 1.717e+02 | 2.757e+04 | 2.787e+04
24.0 | 1.564e+02 | 2.059e+02 | 3.608e+04 | 3.645e+04
25.6 | 1.823e+02 | 1.849e+02 | 4.702e+04 | 4.738e+04
27.2 | 2.277e+02 | 2.281e+02 | 5.910e+04 | 5.956e+04
28.8 | 3.315e+02 | 4.441e+02 | 7.819e+04 | 7.896e+04
30.4 | 5.277e+02 | 5.347e+02 | 1.108e+05 | 1.119e+05
32.0 | 8.749e+02 | 5.337e+02 | 1.634e+05 | 1.648e+05
33.6 | 1.333e+03 | 5.148e+02 | 2.441e+05 | 2.460e+05
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

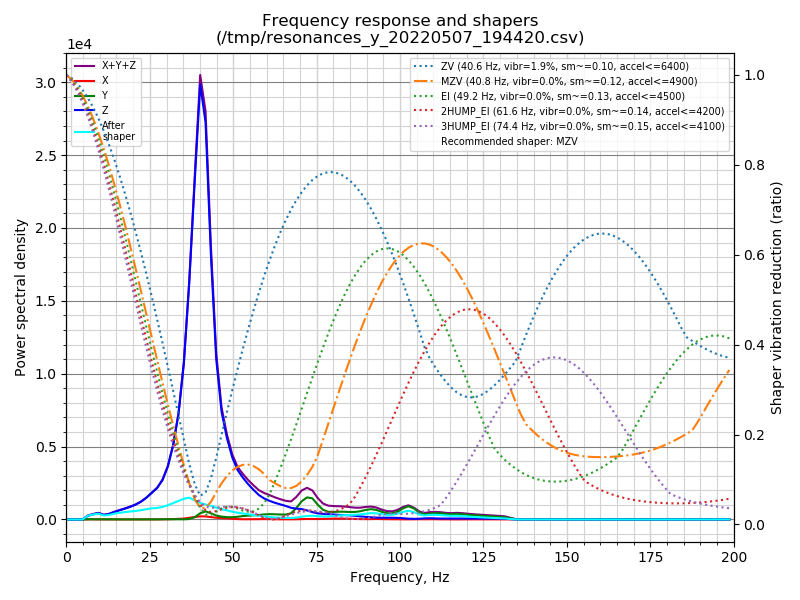
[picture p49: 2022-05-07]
resonance_testing/shaper_calibrate_y.png

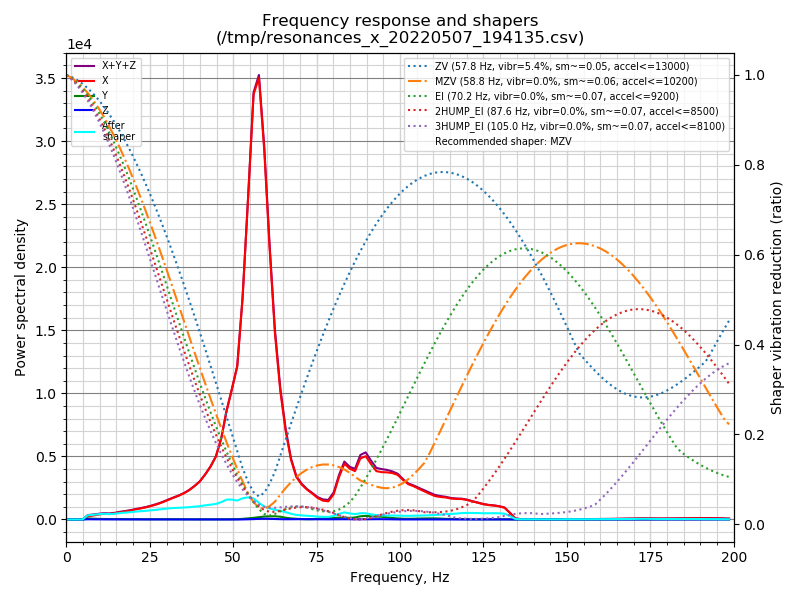
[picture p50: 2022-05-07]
resonance_testing/shaper_calibrate_x.png

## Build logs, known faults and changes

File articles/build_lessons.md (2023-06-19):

# Lessons I learnt during the build, but wish I didn't need to
Your mileage may vary - some of this will probably be very obvious to others (I hope so!)

In no particular order:
- It is a journey and not a destination - you are never really finished - every Klipper update is an adventure
- The command prompt is you friend - on your computer, on the Raspi, using Klipper
- It will almost certainly be cheaper and easier to buy an finished printer (eg Prusa Mk 4 or BambuLabs XC1 or P1P) than to build, mod, fix, rinse and repeat

- ALL the motor directions had to be swapped in the example config file from Voron Design. That's fine, but half of the z-axis motor are opposite directions, so getting them all inverted was not obvious
- Lubricate the rails prior to installation, seriously
- Set the z-axis rails just a little more above the bottom (spec'd as 3mm) otherwise fitting the belt covers is a real pain
- Obsess over a square frame. I assembled mine once reasonably well, then carried it to my only really flat surface, the stone kitchen bench, and resquared it all, then went through and rail by rail put locktite on all the screws as I reinstalled them. It seems to have stayed square
- De-rack the XY axis - the manual mentions it, but until I found this video (XXX) on the Voron site, I was not doing it right
- A few people talk about XY belt tensions, not a lot about Z - set them all to ~110-120Hz using some phone app. When you pluck them they will all sound the same
- After a particular update to klipper (v0.10.0-546) or maybe it was the RPi (4) update it started randomly disconnecting from WiFi after about 10 minutes. Lots of ideas on how to fix it... in [this](https://community.octoprint.org/t/octopi-losing-network-connection-mid-print/16315/163) very long thread and I ended up adding this [cron job](https://gist.github.com/jacobpretorius/1c479ec38e8021196215fd2e9ae74675)
```
sudo crontab -e
*/5 * * * * /bin/ping -q -c10 192.168.8.1 > /dev/null 2>&1 || (ip link set dev wlan0 down ;ip link set dev wlan0 up ;/usr/bin/logger wifi on wlan0 restarted via crontab)
```
- to check if it is restarting the WiFi check the syslog ` tail -10 /var/log/syslog `

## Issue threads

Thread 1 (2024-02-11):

Thermal fuse on the chamber heater?

soostdijck, 2024-02-11:
Nice find for the ready made chamber heater, I'm about to go order the same one.

Just curious, where and how did you mount the thermal fuse for it, if any? What's the hold temp you went for? I'm thinking 90 should be ok'ish.

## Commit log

2023-01-26 Update README.md
    Changed the extruder - LGX Lite does not grip well enough on uneven filaments
    Added temperature display macro for neoLEDS
    New mount for BTT EBB36 board
2023-05-10 Update my_setup.md
    Added links for cable clips
2023-05-14 Update my_setup.md
    Finalised wiring for hotend fan monitor with signal diode inline
2023-06-14 Update my_setup.md
    Updated with Phaetus Rapido Plus hotend
2023-06-15 Update README.md
    Added details on filament dryer
2023-06-16 Update my_setup.md
    Moved the klipper updating guide to a separate file
2023-06-19 Update README.md
    Added info on toolhead offset adjustment
2023-06-26 Update README.md
    Changed the pictures to the current build including KlipperScreen
2023-06-29 Update my_setup.md
    Added info on active heating
